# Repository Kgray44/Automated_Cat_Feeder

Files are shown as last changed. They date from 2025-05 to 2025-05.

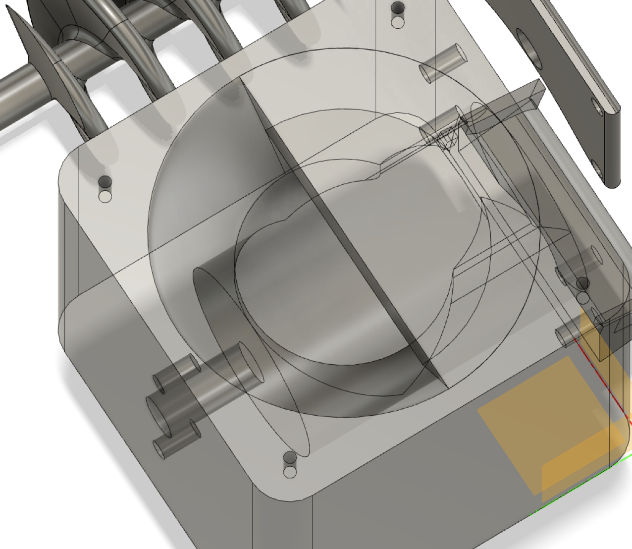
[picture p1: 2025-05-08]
Pictures/3D/image.png

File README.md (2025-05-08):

# Automated_Cat_Feeder
An automated cat feeder project based on an ESP32!

## Project Components
* DRV8874 motor driver
* TPS65261 3-channel voltage regulator
* ESP32-S3-WROOM-1 with 8MB RAM
* OV2640 camera
* I2C OLED Display

## Project Overview
* Feeds cats using an auger design
* Has a food hopper for long term dispension
* Automated system with schedule and facial recognition
* Manual option for feeding immediately
* Utilizes WiFi for UI and obtaining the current time
* Smooth WiFi setup interface for new networks

## Project Status (as of 5/8/25)
* Partially working auger system for dispensing
* Working motor driver / motor system with current feedback
* Working jam detection using current feedback from motor
* Easy to use web interface containing settings; feed time length, a schedule (4x a day max), a change password page, a page to reset device or erase memory, and a page to update software, etc.
* Smooth WiFi setup for first time network connection with multiple fallbacks
* Working OLED display displaying feeder status

## How to Use
Upload the code from the respository to your cat feeder board.  Power up the device and then refer to the 'WiFi Setup' section for next steps.

## Project Description

### WiFi Setup
When first turning the system on, the board will check its flash for a saved network.  If there is a saved network, it will attempt to connect to it. If it can't connect after 30 sec, it will erase the saved network from flash, and restart itself.  If there is no saved network in flash, it will start an access point network called 'catfeeder_AP'.  After connecting to this network with your smartphone (laptop/dekstop works as well, but you must go to '192.168.4.1' in a browser), a captive portal will come up requiring you to put in a network name and password.  After you have entered these, the device will reboot, and attempt to connect to that network.

### User Interface (website)
If the WiFi connection is successful, go to 'catfeeder.local' in a browser, and a webpage will open requiring you to signin.  Trying to visit any of the feeder's webpages without signing in will kick you back to the signin page.  After successfully signing in, the home page will load which contains a menu bar, two main settings, and a 'feed now' button.  There is also an LED indicator that will turn green when the motor is running, and stay red when not.

All webpages that you open on this webpage will be loaded next to the homepage dynamically.  The page will never reload, nor should you need to reload it for any reason.  All data and pages are delivered dynamically and updated automatically.

### Siri Integration (for iPhone/Mac)
By adding a shortcut to your device, you can use "Hey Siri" to turn the feeder on*.  It utilizes the cookie authentication to be able to turn the device on with the '/feed' endpoint.  To call this shortcut, say "Hey Siri" and then the shortcut name.  I named my shortcut 'Feed my Cats', so I would say "Hey Siri, feed my cats".
Visit this link to retrieve the shortcut: https://www.icloud.com/shortcuts/d3358b3d90564f18b419d0107f0d7751

*Please note this only works when on the same WiFi network as the feeder itself.

## Unfinished Components / Issues (as of 5/8/25)
* I am still working on getting the camera to work, so no facial recognition or camera code is added yet
* Auger currently jams due to bad screw design
* OLED Display displays "feeding" even when not feeding
* Food measurement is currently in seconds the auger turns, instead of grams of food
* A small box appears next to the homepage after going to another webpage and going back

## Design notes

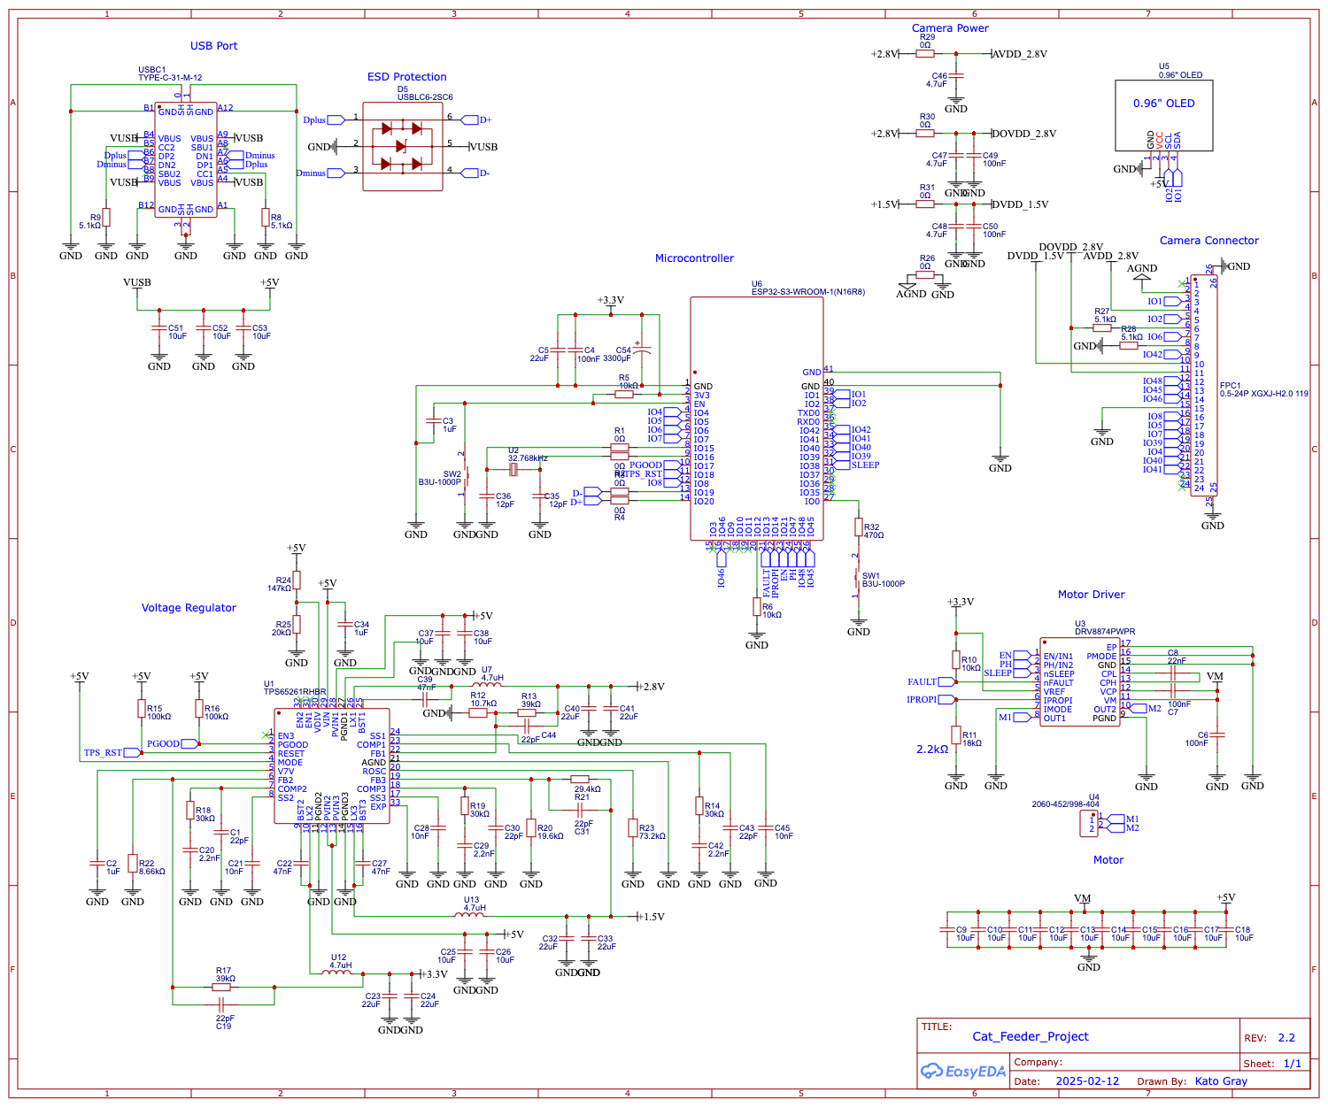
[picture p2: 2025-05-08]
design_files/schematic/Schematic_Cat Feeder Project 2_2025-05-08.png

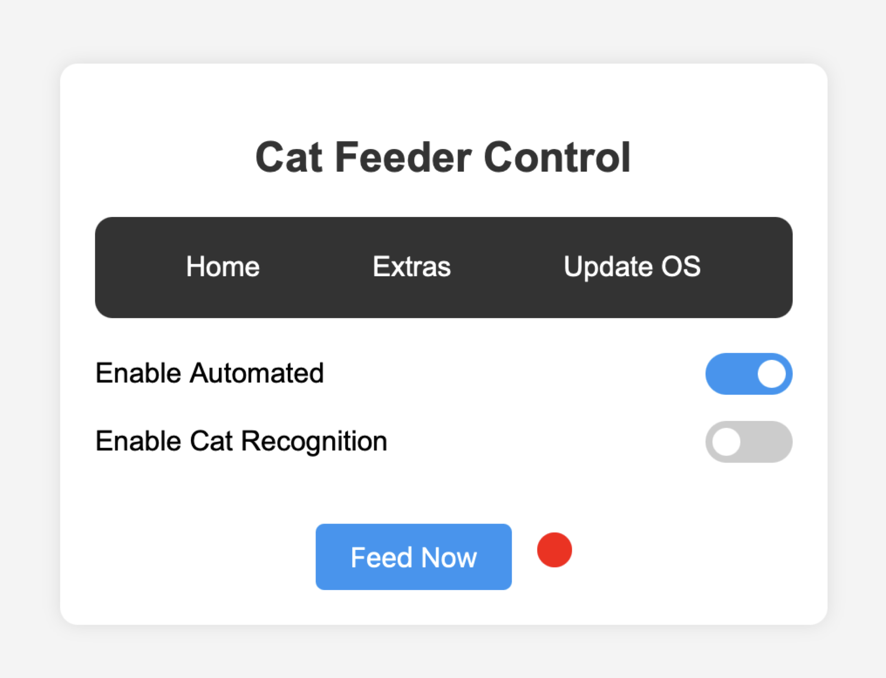
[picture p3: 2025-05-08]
Pictures/website/homepage.png

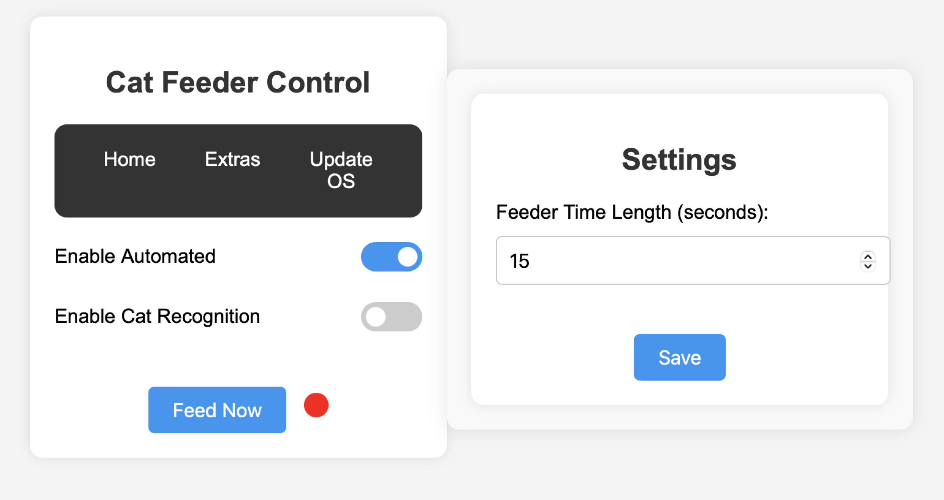
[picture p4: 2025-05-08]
Pictures/website/image.png

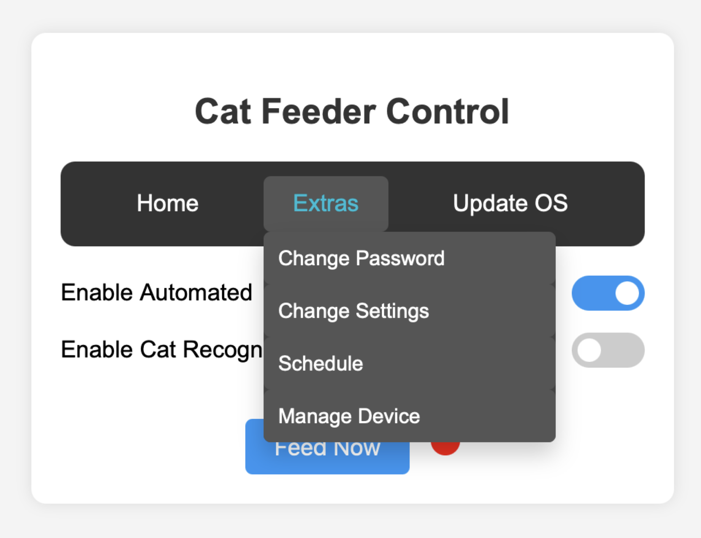
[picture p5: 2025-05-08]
Pictures/website/menu.png

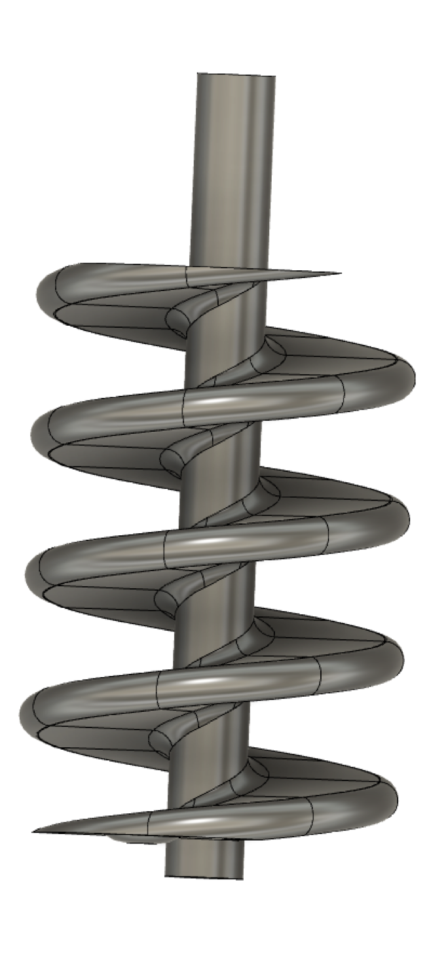
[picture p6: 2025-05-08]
Pictures/3D/screw.png

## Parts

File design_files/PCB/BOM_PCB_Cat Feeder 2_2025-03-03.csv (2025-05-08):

ID | Name | Designator | Footprint | Quantity | Manufacturer Part | Manufacturer | Supplier | Supplier Part | Price
1 | 22pF | C1,C19,C30,C31,C43,C44 | C0402 | 6 | CC0402GRNPO9BN220 | YAGEO(国巨) | LCSC | C541412 | 0.002
2 | 1uF | C2,C3,C34 | C0402 | 3 | CL05A105KO5NNNC | SAMSUNG(三星) | LCSC | C29266 | 0.002
3 | 100nF | C4,C6,C7,C49,C50 | C0402 | 5 | CL05B104KO5NNNC | SAMSUNG(三星) | LCSC | C1525 | 0.001
4 | 22nF | C8 | C0402 | 1 | GRM155R71E223JA61D | muRata(村田) | LCSC | C426639 | 0.011
5 | 2.2nF | C20,C29,C42 | C0402 | 3 | CC0402JRX7R9BB222 | YAGEO(国巨) | LCSC | C513667 | 0.002
6 | 10nF | C21,C28,C45 | C0402 | 3 | CC0402JRX7R9BB103 | YAGEO(国巨) | LCSC | C272878 | 0.002
7 | 47nF | C22,C27,C39 | C0402 | 3 | 0402B473K500NT | FH(风华) | LCSC | C82219 | 0.002
8 | 12pF | C35,C36 | C0402 | 2 | GCM1555C1H120FA16D | muRata(村田) | LCSC | C393682 | 0.018
9 | 22uF | C5 | C0603 | 1 | CL10A226MP8NUNE | SAMSUNG(三星) | LCSC | C86295 | 0.012
10 | 10uF | C25,C26,C37,C38,C51,C52,C53 | C0603 | 7 | CL10A106KP8NNNC | SAMSUNG(三星) | LCSC | C19702 | 0.006
11 | 4.7uF | C46,C47,C48 | C0603 | 3 | CL10A475KP8NNNC | SAMSUNG(三星) | LCSC | C1705 | 0.004
12 | 10uF | C9,C10,C11,C12,C13,C14,C15,C16,C17,C18 | C0805 | 10 | CL21A106KBYQNNE | SAMSUNG(三星) | LCSC | C2932476 | 0.05
13 | 22uF | C23,C24,C32,C33,C40,C41 | C0805 | 6 | CL21A226MOQNNNE | SAMSUNG(三星) | LCSC | C98190 | 0.019
14 | USBLC6-2SC6 | D5 | SOT-23-6_L2.9-W1.6-P0.95-LS2.8-BL | 1 | USBLC6-2SC6 | ST(意法半导体) | LCSC | C7519 | 0.111
15 | 0.5-24P XGXJ-H2.0 119 | FPC1 | FPC-SMD_24P-P0.50_SHOU-HAN_XGXJ-H2.0 | 1 | 0.5-24P XGXJ-H2.0 119 | SHOU HAN(首韩) | LCSC | C2858298 | 0.101
16 | 0Ω | R1,R2,R3,R4,R26,R29,R30,R31 | R0402 | 8 | 0402WGF0000TCE | UNI-ROYAL(厚声) | LCSC | C17168 | 0.001
17 | 10kΩ | R5,R6,R10 | R0402 | 3 | 0402WGJ0103TCE | UNI-ROYAL(厚声) | LCSC | C25531 | 0.001
18 | 5.1kΩ | R8,R9,R27,R28 | R0402 | 4 | 0402WGF5101TCE | UNI-ROYAL(厚声) | LCSC | C25905 | 0.001
19 | 18kΩ | R11 | R0402 | 1 | RT0402BRD0718KL | YAGEO(国巨) | LCSC | C852579 | 0.021
20 | 10.7kΩ | R12 | R0402 | 1 | PTFR0402B10K7N9 | RESI(开步睿思) | LCSC | C2693084 | 0.109
21 | 39kΩ | R13,R17 | R0402 | 2 | RC0402FR-0739KL | YAGEO(国巨) | LCSC | C137995 | 0.001
22 | 30kΩ | R14,R18,R19 | R0402 | 3 | RC0402FR-0730KL | YAGEO(国巨) | LCSC | C138008 | 0.001
23 | 100kΩ | R15,R16 | R0402 | 2 | RC0402FR-07100KL | YAGEO(国巨) | LCSC | C60491 | 0.001
24 | 19.6kΩ | R20 | R0402 | 1 | RT0402BRD0719K6L | YAGEO(国巨) | LCSC | C852589 | 0.021
25 | 29.4kΩ | R21 | R0402 | 1 | 0402WGF2942TCE | UNI-ROYAL(厚声) | LCSC | C26973 | 0.001
26 | 8.66kΩ | R22 | R0402 | 1 | FRC0402F8661TS | FOJAN(富捷) | LCSC | C5126133 | 0.001
27 | 73.2kΩ | R23 | R0402 | 1 | RT0402BRD0773K2L | YAGEO(国巨) | LCSC | C852909 | 0.02
28 | 147kΩ | R24 | R0402 | 1 | 0402WGF1473TCE | UNI-ROYAL(厚声) | LCSC | C64171 | 0.001
29 | 20kΩ | R25 | R0402 | 1 | RC0402FR-0720KL | YAGEO(国巨) | LCSC | C93942 | 0.001
30 | 470Ω | R32 | R0402 | 1 | RC0402FR-07470RL | YAGEO(国巨) | LCSC | C114877 | 0.001
31 | B3U-1000P | SW1 | KEY-SMD_B3U-1000PM | 1 | B3U-1000P | OMRON(欧姆龙) | LCSC | C231329 | 0.159
32 | TPS65261RHBR | U1 | VQFN-32_L5.0-W5.0-P0.50-TL-EP | 1 | TPS65261RHBR | TI(德州仪器) | LCSC | C138722 | 0.548
33 | 32.768kHz | U2 | CRYSTAL-SMD_L3.2-W1.5 | 1 | FC31M2-32.768-NTLNNDTL | HCI(杭晶) | LCSC | C5120559 | 0.19
34 | DRV8874PWPR | U3 | HTSSOP-16_L5.0-W4.4-P0.65-LS6.4-BL-EP | 1 | DRV8874PWPR | TI(德州仪器) | LCSC | C1855818 | 0.88
35 | 2060-452/998-404 | U4 | CONN-SMD_2060-452 | 1 | 2060-452/998-404 | WAGO(万可) | LCSC | C2765055 | 0.236
36 | 0.96" OLED | U5 | CONN-TH_PZ2.54-1X4-11.2 | 1
37 | ESP32-S3-WROOM-1(N16R8) | U6 | WIRELM-SMD_ESP32-S3-WROOM-1 | 1 | ESP32-S3-WROOM-1-N16R8 | ESPRESSIF(乐鑫) | LCSC | C2913202 | 5.774
38 | 4.7uH | U7,U12,U13 | IND-SMD_L5.2-W5.2_MS0530-XX | 3 | MDA5030-4R7M | KOHERelec(科或) | LCSC | C2847477 | 0.825
39 | TYPE-C-31-M-12 | USBC1 | USB-C_SMD-TYPE-C-31-M-12 | 1 | TYPE-C-31-M-12 | 韩国韩荣 | LCSC | C165948 | 0.175

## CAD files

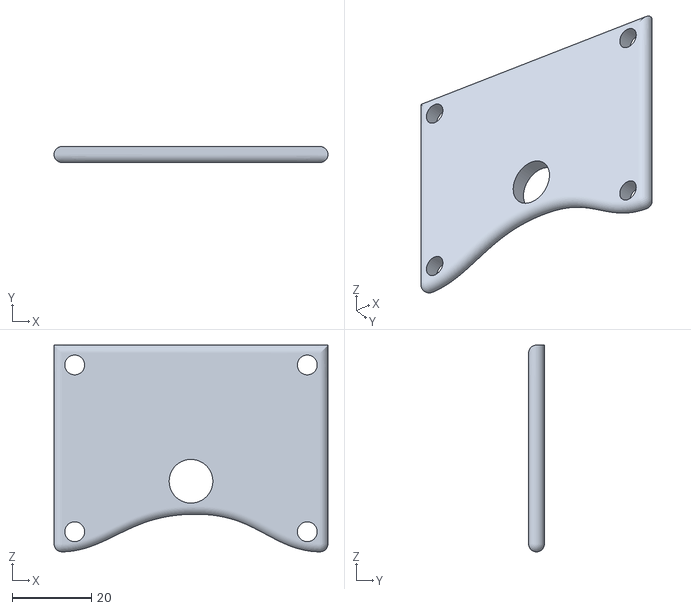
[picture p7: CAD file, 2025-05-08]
design_files/3D_fusion/Lid.stl
69.0 x 4.00 x 52.1

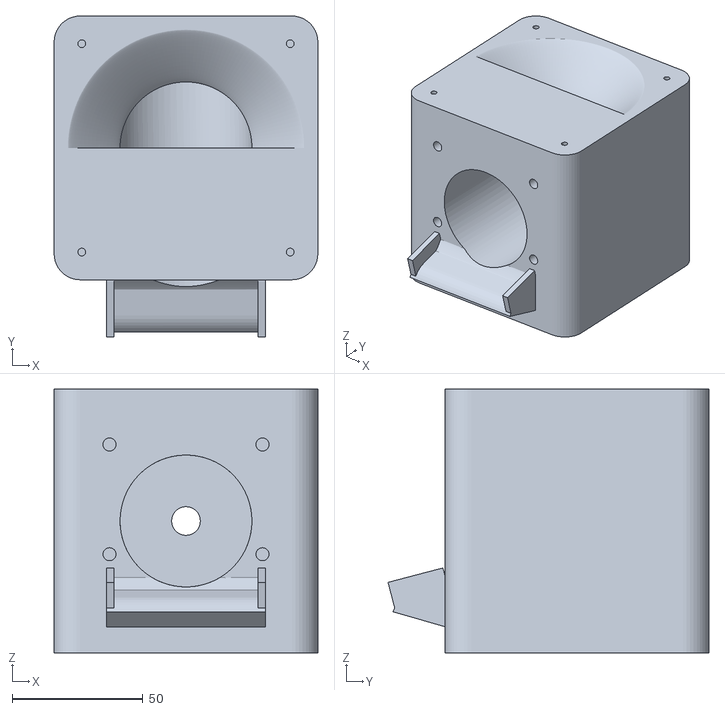
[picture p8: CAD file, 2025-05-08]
design_files/3D_fusion/Body1 (new).stl
101.0 x 122.9 x 101.0

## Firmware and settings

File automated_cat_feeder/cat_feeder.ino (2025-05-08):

#include <WiFi.h>
#include <WiFiAP.h>
#include "esp_wifi.h"
#include <DNSServer.h>
#include <HTTPClient.h>
#include <AsyncTCP.h>
#include <ESPAsyncWebServer.h>
#include <Update.h>
#include <ESPmDNS.h>
#include <ArduinoJson.h>
#include <map>
#include <vector>
#include <time.h>
#include <Preferences.h>
#include <SPI.h>
#include <Wire.h>
#include <Adafruit_GFX.h>
#include <Adafruit_SSD1306.h>
#include <Fonts/FreeSerif9pt7b.h>

#include "html.h"
#include "bitmap_icons.h"

//motor driver pins
#define PGOOD     17  //IO17
#define PRST      18  //IO18
#define sleep_pin 38  //IO38
#define en_pin    21  //IO21
#define ph_pin    47  //IO47
#define fault_pin 13  //IO13
#define ipropi    14  //IO14

#define SCREEN_WIDTH    128   // OLED display width, in pixels
#define SCREEN_HEIGHT   64    // OLED display height, in pixels
#define OLED_RESET      -1    // Reset pin # (or -1 if sharing Arduino reset pin)
#define SCREEN_ADDRESS  0x3C ///< See datasheet for Address; 0x3D for 128x64, 0x3C for 128x32
#define SDA 1
#define SCL 2

#define jamcurrent 350 //current in mA for jam
#define jamFixAttemptLimit 10 //number of attempts to fix the jam

bool jammed = false;
int jamFixAttempt = 0;
float smoothedCurrent_mA = 0;
float smoothingFactor = 0.1;  // smaller = smoother

// Wi-Fi Configuration
const char* ssid = "";//don't fill
const char* password = "";//don't fill
const char* ap_ssid = "catfeeder_AP";
const char* ap_password = "makers4ever";

// Login credentials
const char* login_username = "cats";
const char* login_password = "maker";

bool automated = false;
bool cat_recognition = false;
bool motorOn = false;
bool feeder_on = false;
unsigned long startmillis = 0;
unsigned long lastms2 = 0;
unsigned long scheduleMillis = 0;
unsigned long setupmillis = 0;
unsigned long internetmillis = 0;
unsigned long lastSend = 0;
int motorTime = 5;

bool tog=false;
bool printed=false;

//WiFi AP
const byte DNS_PORT = 53;
IPAddress apIP(192, 168, 4, 1); // SoftAP IP
DNSServer dnsServer;

Adafruit_SSD1306 display(SCREEN_WIDTH, SCREEN_HEIGHT, &Wire, OLED_RESET);

// Async Web Server
AsyncWebServer server(80);
AsyncWebSocket ws("/ws");

bool isAuthenticated(AsyncWebServerRequest *request) {
  if (request->hasHeader("Cookie")) {
    String cookie = request->header("Cookie");
    if (cookie.indexOf("ESPSESSIONID=1") != -1) {
      return true;
    }
  }
  return false;
}

void notifyClients() {
  String json = "{\"automated\":";
  json += automated ? "true" : "false";
  json += ",\"cat_recognition\":";
  json += cat_recognition ? "true" : "false";
  json += ",\"motorOn\":";
  json += motorOn ? "true" : "false";
  json += ",\"current\":";
  json += smoothedCurrent_mA;
  json += "}";
  ws.textAll(json);
  Serial.println(json);
}

void handleWebSocketMessage(void *arg, uint8_t *data, size_t len) {
  AwsFrameInfo *info = (AwsFrameInfo *)arg;
  if (info->final && info->index == 0 && info->len == len && info->opcode == WS_TEXT) {
    data[len] = 0;
    if (strcmp((char *)data, "toggleAutomated") == 0) {
      Serial.println("toggleAutomated");
    } else if (strcmp((char *)data, "toggleCat_recognition") == 0) {
      Serial.println("toggleCat_recognition");
    } else if (strcmp((char *)data, "getStatus") == 0) {
      // If the client requests the status, send it
      notifyClients();
      Serial.println("Sent status update to client");
    }
    notifyClients();
    Serial.println("handled websocket message...");
  }
}

void onEvent(AsyncWebSocket *server, AsyncWebSocketClient *client, AwsEventType type,
             void *arg, uint8_t *data, size_t len) {
  switch (type) {
    case WS_EVT_CONNECT:
      Serial.println("WebSocket client connected");
      notifyClients();
      break;
    case WS_EVT_DISCONNECT:
      Serial.println("WebSocket client disconnected");
      break;
    case WS_EVT_DATA:
      handleWebSocketMessage(arg, data, len);
      break;
    case WS_EVT_PONG:
    case WS_EVT_ERROR:
      break;
  }
}

String makeScheduleRows() {
  String days[] = {"Sun","Mon","Tue","Wed","Thu","Fri","Sat"};
  String html;
  for (int d = 0; d < 7; d++) {
    html += "<tr><td>" + days[d] + "</td><td class='time-slot'>";
    for (int i = 0; i < 4; i++) {
      html += "<input type='time' id='" + days[d] + String(i) + "' name='" + days[d] + String(i) + "'>";
    }
    html += "</td></tr>";
  }

  return html;
}

String schedule_processor(const String& var) {
  if (var == "SCHEDULE_ROWS") {
    String rows = makeScheduleRows();
    return String(rows);
  }
  return String(); // Return empty string for unknown placeholders
}

/*String motortime_processor(const String& var) {
  if (var == "MOTORTIME"){
    return String(motorTime);
  }
  return String();
}*/

bool checkInternet() {
  if (WiFi.status() != WL_CONNECTED) return false;

  HTTPClient http;
  http.setConnectTimeout(3000);  // 3 sec timeout
  http.begin("http://clients3.google.com/generate_204");  // Lightweight, returns 204
  int code = http.GET();
  http.end();

  return (code == 204);
}

std::map<String, std::vector<String>> feedingSchedule;
Preferences prefs;

void setup() {
  Serial.begin(115200);
  esp_reset_reason_t reason = esp_reset_reason();
  Serial.printf("\nReset reason: %d → ", reason);
  switch (reason) {
    case ESP_RST_POWERON:      Serial.println("POWERON_RESET"); break;
    case ESP_RST_EXT:          Serial.println("EXT_RESET"); break;
    case ESP_RST_SW:           Serial.println("SW_RESET"); break;
    case ESP_RST_PANIC:        Serial.println("PANIC_RESET"); break;
    case ESP_RST_INT_WDT:      Serial.println("INT_WDT_RESET"); break;
    case ESP_RST_TASK_WDT:     Serial.println("TASK_WDT_RESET"); break;
    case ESP_RST_WDT:          Serial.println("OTHER_WDT_RESET"); break;
    case ESP_RST_DEEPSLEEP:    Serial.println("DEEPSLEEP_RESET"); break;
    case ESP_RST_BROWNOUT:     Serial.println("BROWNOUT_RESET"); break;
    case ESP_RST_SDIO:         Serial.println("SDIO_RESET"); break;
    case ESP_RST_USB:          Serial.println("USB_RESET"); break;
    default:                   Serial.println("UNKNOWN"); break;
  } 

  Wire.begin(SDA, SCL);
  delay(100);

  if(!display.begin(SSD1306_SWITCHCAPVCC, SCREEN_ADDRESS)) {
    Serial.println(F("SSD1306 allocation failed"));
  }
  //display.setFont(&FreeSerif9pt7b);
  display.clearDisplay();

  pinMode(sleep_pin, OUTPUT);
  pinMode(en_pin, OUTPUT);
  pinMode(ph_pin, OUTPUT);
  pinMode(fault_pin, INPUT);
  pinMode(ipropi, INPUT);
  pinMode(PGOOD, INPUT);
  pinMode(PRST, INPUT);

  digitalWrite(sleep_pin, LOW);//turn sleep on
  //digitalWrite(en_pin, HIGH);//enable
  Serial.println("Pins setup complete!\nStarting WiFi...");

  //load saved data from flash memory
  loadSavedData();

  if (strlen(ssid) > 0){
    // Initialize Wi-Fi
    WiFi.mode(WIFI_STA);
    WiFi.begin(ssid, password);
    setupmillis = millis();
    Serial.print("Connecting to WiFi");
    while (WiFi.status() != WL_CONNECTED) {
      delay(500);
      Serial.print(".");
      if (tog){printCentered("WiFi STA .");} else {printCentered("WiFi STA  ");}
      tog=!tog;
      if (millis() - setupmillis > 20000){//20 seconds not connecting
        prefs.begin("wifi_network", false);
        prefs.putString("ssid", "");
        prefs.putString("pass", "");
        prefs.end();

        Serial.println("Rebooting now due to failed connection...");
        printCentered("Failed connection!");
        delay(2000);
        ESP.restart();
      }
    }
    Serial.println("\nConnected to WiFi");
    Serial.println("IP Address:");
    Serial.println(WiFi.localIP());
    printCentered("WiFi Connected\n'catfeeder.local'");
    delay(500);
  
  // Set time zone and NTP server
  //configTzTime("EST5EDT,M3.2.0/2,M11.1.0/2", "pool.ntp.org", "time.nist.gov");
  configTime(-4 * 3600, 0, "pool.ntp.org", "time.nist.gov");
  Serial.print("Waiting for time sync");

  setupmillis = millis();
  time_t now = time(nullptr);

  while (now < 8 * 3600 * 2 && (millis() - setupmillis < 20000)) {
    if (tog){printCentered("WiFi Connected\n'catfeeder.local'\nTime sync .");} else {printCentered("WiFi Connected\n'catfeeder.local'\nTime sync  ");}
    tog=!tog;
    delay(500);
    Serial.print(".");
    now = time(nullptr);
  }

  if (now < 8 * 3600 * 2) {
    Serial.println("\n Time sync failed after 20 seconds.");
    printCentered("Time sync failed!");
    delay(2000);
  } else {
    Serial.println("\n Time synchronized.");
    printCentered("WiFi Connected\n'catfeeder.local'\nTime sync success!");
    struct tm* t = localtime(&now);
    char currentTime[6];
    sprintf(currentTime, "%02d:%02d", t->tm_hour, t->tm_min);
    Serial.println(currentTime);
  }

  ws.onEvent(onEvent);
  server.addHandler(&ws);

  server.on("/", HTTP_GET, [](AsyncWebServerRequest *request) {
    if (isAuthenticated(request)) {
      request->redirect("/index");
      notifyClients();
    } else {
      request->send_P(200, "text/html", login_html);
    }
  });

  // Route to Handle Login
  server.on("/login", HTTP_POST, [](AsyncWebServerRequest *request) {
    if (request->hasParam("username", true) && request->hasParam("password", true)) {
      String username = request->getParam("username", true)->value();
      String password = request->getParam("password", true)->value();
      if (username == login_username && password == login_password) {
        AsyncWebServerResponse *response = request->beginResponse(301);
        response->addHeader("Set-Cookie", "ESPSESSIONID=1; HttpOnly");
        response->addHeader("Location", "/index");
        request->send(response);
      } else {
        request->send(401, "text/plain", "Unauthorized");
      }
    }
  });

  // Route for Control Page
  server.on("/index", HTTP_GET, [](AsyncWebServerRequest *request) {
    if (isAuthenticated(request)) {
      request->send_P(200, "text/html", index_html);
      notifyClients();
    } else {
      request->redirect("/");
    }
  });

  //route for password change
  server.on("/change", HTTP_GET, [](AsyncWebServerRequest *request) {
    if (isAuthenticated(request)) {
      request->send_P(200, "text/html", change_html);
    } else {
      request->redirect("/");
    }
  });

  server.on("/save-change", HTTP_POST, [](AsyncWebServerRequest *request) {
    if (request->hasParam("password", true) && request->hasParam("passwordd", true)) {
      String password = request->getParam("password", true)->value();
      String passwordd = request->getParam("passwordd", true)->value();

      if (password == passwordd) {
        // Save the new password logic here
        login_password = password.c_str();
        prefs.begin("auth", false);
        prefs.putString("password", login_password);
        prefs.end();
        request->send(200, "text/plain", "Password successfully changed.");
      } else {
        request->send(400, "text/plain", "Passwords do not match.");
      }
    } else {
      request->send(400, "text/plain", "Missing parameters.");
    }
  });

  //route for settings
  server.on("/settings", HTTP_GET, [](AsyncWebServerRequest *request) {
    if (isAuthenticated(request)) {
      request->send(200, "text/html", settings_html);
    } else {
      request->redirect("/");
    }
  });

  server.on("/save-settings", HTTP_POST, [](AsyncWebServerRequest *request) {
    if (!isAuthenticated(request)) {
      request->send(401, "text/plain", "Unauthorized");
      return;
    }

    if (request->hasParam("motorTime", true)) {
      String motorTimeR = request->getParam("motorTime", true)->value();
      motorTime = motorTimeR.toInt();
      Serial.println("Motor Time Length updated to: " + String(motorTime));

      prefs.begin("settings", false); // namespace = "settings", readWrite = false
      prefs.putInt("motorTime", motorTime);
      prefs.end();

      request->send(200, "text/plain", "Settings saved successfully!");
      //request->redirect("/index");
    } else {
      request->send(400, "text/plain", "Motor Time Length not provided");
    }
  });

  server.on("/api/motortime", HTTP_GET, [](AsyncWebServerRequest *request){
    if (!isAuthenticated(request)) {
      request->send(401, "application/json", "{\"error\":\"unauthorized\"}");
      return;
    }
    request->send(200, "application/json", "{\"motorTime\":" + String(motorTime) + "}");
  });

  /*server.on("/schedule", HTTP_GET, [](AsyncWebServerRequest *request){
    if (!isAuthenticated(request)) {
      request->redirect("/");
      return;
    }
    String html = String(schedule_html);
    html.replace("%SCHEDULE_ROWS%", makeScheduleRows());
    request->send(200, "text/html", html);
  });*/
  server.on("/schedule", HTTP_GET, [](AsyncWebServerRequest *request){
    if (!isAuthenticated(request)) {
      request->redirect("/");
      return;
    }
    request->send(200, "text/html", schedule_html, schedule_processor);
  });


  server.on("/save-schedule", HTTP_POST, [](AsyncWebServerRequest *request){
    if (!isAuthenticated(request)) {
      request->send(401, "text/plain", "Unauthorized");
      return;
    }
  }, NULL, [](AsyncWebServerRequest *request, uint8_t *data, size_t len, size_t index, size_t total) {
    StaticJsonDocument<2048> doc;
    DeserializationError error = deserializeJson(doc, data, len);

    if (error) {
      request->send(400, "text/plain", "Bad JSON");
      return;
    }

    feedingSchedule.clear();

    for (JsonPair kv : doc.as<JsonObject>()) {
      String day = kv.key().c_str();
      JsonArray times = kv.value().as<JsonArray>();
      for (JsonVariant v : times) {
        feedingSchedule[day].push_back(v.as<String>());
      }
    }
    // 🔒 Save entire schedule JSON to NVS (flash)
    prefs.begin("schedule", false);
    String jsonString;
    serializeJson(doc, jsonString);
    prefs.putString("feedmap", jsonString);
    prefs.end();

    request->send(200, "text/plain", "Schedule saved");
  });
  
  server.on("/api/schedule", HTTP_GET, [](AsyncWebServerRequest *request){
    if (!isAuthenticated(request)) {
      request->send(401, "application/json", "{\"error\":\"unauthorized\"}");
      return;
    }

    StaticJsonDocument<2048> doc;

    for (auto const& kv : feedingSchedule) {
      JsonArray arr = doc.createNestedArray(kv.first);
      for (auto const& time : kv.second) {
        arr.add(time);
      }
    }

    String response;
    serializeJson(doc, response);
    request->send(200, "application/json", response);
  });

  server.on("/reset-schedule", HTTP_POST, [](AsyncWebServerRequest *request){
    if (!isAuthenticated(request)) {
      request->send(401, "text/plain", "Unauthorized");
      return;
    }

    feedingSchedule.clear();  // Clear the stored schedule
    Serial.println("Schedule has been reset.");
    request->send(200, "text/plain", "Schedule reset");
  });

  server.on("/manage", HTTP_GET, [](AsyncWebServerRequest *request) {
    if (isAuthenticated(request)) {
      request->send_P(200, "text/html", manage_html);
    } else {
      request->redirect("/");
    }
  });

  server.on("/reset", HTTP_POST, [](AsyncWebServerRequest *request) {
    if (isAuthenticated(request)) {
      prefs.begin("settings", false); prefs.clear(); prefs.end();
      prefs.begin("schedule", false); prefs.clear(); prefs.end();
      prefs.begin("auth", false); prefs.clear(); prefs.end();
      request->send(200, "text/plain", "Memory erased!");
    } else {
      request->send(401);
    }
  });

  server.on("/restart", HTTP_POST, [](AsyncWebServerRequest *request) {
    if (isAuthenticated(request)) {
      request->send(200, "text/plain", "Restarting...");
      delay(100);  // Ensure response is sent
      ESP.restart();
    } else {
      request->send(401);
    }
  });
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
void loop() {
  if (WiFi.getMode() != WIFI_STA){
    printCentered("Waiting for cred");
    dnsServer.processNextRequest();
    return;
  }

  if (jammed){
    ESP.restart();
  }

  if (millis() - internetmillis > 10000){//check for internet every ten seconds
    if (!checkInternet()) {//if no internet, restart
      prefs.begin("wifi_network", false);
      prefs.putString("ssid", "");
      prefs.putString("pass", "");
      prefs.end();
      Serial.println("No internet, restarting and wiping SSID&PASS...");
      printCentered("Internet failed");
      delay(1000);
      ESP.restart();
    }
    internetmillis = millis();
  }

  ws.cleanupClients();
  delay(50);
  yield();
  if (startmillis != 0 && millis() - startmillis > motorTime*1000) {
    digitalWrite(sleep_pin, LOW);//turn sleep on
    digitalWrite(en_pin, LOW);//disable
    motorOn = false;
    Serial.println("Feeder motor off");
    notifyClients();
    printed=false;
    startmillis = 0;
  }

  if (automated){
    checkSchedule();
  }

  if (millis() - lastSend >= 100) {
    if (motorOn){
      if (!printed){printCentered("Feeding ");printed=true;}
      if (tog){display.drawBitmap(60, 24, motor1Char, 5, 8, WHITE);display.display();} else {display.drawBitmap(60, 24, motor1Char, 5, 8, WHITE);display.display();}
      tog=!tog;
      float adcVoltage = analogRead(ipropi) * (3.3 / 4095.0); // volts
      float motorCurrent = adcVoltage / (0.000455 * 2700.0);      // amps
      //motorCurrent = motorCurrent*1000; //ma
      smoothedCurrent_mA = smoothedCurrent_mA * (1.0 - smoothingFactor) + (motorCurrent * 1000.0) * smoothingFactor;

      if (smoothedCurrent_mA >= jamcurrent){
        digitalWrite(ph_pin, LOW);//direction backwards
        delay(1000);
        digitalWrite(ph_pin, HIGH);//direction backwards
        delay(500);
        jamFixAttempt++;
        if (jamFixAttempt >= jamFixAttemptLimit){
          jammed = true;
          return;
        }
      }

      notifyClients();  // only stream current if motor is on
      lastSend = millis();
    }
    else { printed=false;display.clearDisplay();jamFixAttempt=0;lastSend = millis();}
  }
  
  /*if (digitalRead(fault_pin) == LOW){
    Serial.println("FAULT");
  }*/
  
  /*if (millis() - lastms2 > 100){
    float adcVoltage = analogRead(ipropi) * (3.3 / 4095.0); // volts
    float motorCurrent = adcVoltage / (0.000455 * 2700.0);      // amps
    Serial.print("Current pin: ");
    Serial.println(motorCurrent*1000,2);
    lastms2 = millis();
  }*/
}

void printCentered(const String& fullText) {
  display.clearDisplay();
  display.setTextWrap(false); // Prevent automatic wrapping

  display.setTextSize(1); // REQUIRED: set font size (1–3 typically)
  display.setTextColor(SSD1306_WHITE);
  display.setFont();      // Use built-in font (optional, but good reset)

  // Step 1: Count lines
  int numLines = 1;
  for (unsigned int i = 0; i < fullText.length(); i++) {
    if (fullText[i] == '\n') numLines++;
  }

  // Step 2: Get height of one line
  int16_t x1, y1;
  uint16_t w, h;
  display.getTextBounds("A", 0, 0, &x1, &y1, &w, &h);
  int lineHeight = h + 2;
  int totalHeight = numLines * lineHeight;

  // Step 3: Y offset
  int yStart = (SCREEN_HEIGHT - totalHeight) / 2;

  // Step 4: Draw each line centered
  String currentLine = "";
  int lineNum = 0;

  for (unsigned int i = 0; i <= fullText.length(); i++) {
    char c = fullText[i];
    if (c == '\n' || i == fullText.length()) {
      display.getTextBounds(currentLine, 0, 0, &x1, &y1, &w, &h);
      int xStart = (SCREEN_WIDTH - w) / 2;

      display.setCursor(xStart, yStart + lineNum * lineHeight);
      display.print(currentLine);

      currentLine = "";
      lineNum++;
    } else {
      currentLine += c;
    }
  }

  display.display();
}



void checkSchedule() {
  time_t now = time(nullptr);
  struct tm* t = localtime(&now);
  char currentTime[6];
  sprintf(currentTime, "%02d:%02d", t->tm_hour, t->tm_min);

  String dayStr[] = {"Sun","Mon","Tue","Wed","Thu","Fri","Sat"};
  auto& todayTimes = feedingSchedule[dayStr[t->tm_wday]];

  for (auto& feedTime : todayTimes) {
    if (millis() - scheduleMillis > 60000){//only one trigger per minute
      String fullMessage = "Next feed time is\n" + feedTime;
      printCentered(fullMessage.c_str());
      if (feedTime == String(currentTime)) {
        Serial.println("Scheduled Feed Triggered at " + String(currentTime));
        feed(); // existing feed() function
        scheduleMillis = millis();
        break;
      }
    }
  }
}

void feed() {
  digitalWrite(sleep_pin, HIGH);//turn sleep off
  digitalWrite(en_pin, HIGH);//enable
  digitalWrite(ph_pin, HIGH);//direction
  motorOn = true;
  startmillis = millis();
  Serial.println("Feeding initiated");
  notifyClients();
}

void loadSavedData(){
  prefs.begin("settings", true); // readOnly = true
  motorTime = prefs.getInt("motorTime", 5); // default to 5 seconds if not set
  automated = prefs.getInt("automated", 0);
  cat_recognition = prefs.getInt("cat_recognition", 0);
  prefs.end();

  prefs.begin("schedule", true);
  String saved = prefs.getString("feedmap", "");
  prefs.end();
  if (saved.length() > 0) {
    StaticJsonDocument<2048> doc;
    DeserializationError error = deserializeJson(doc, saved);
    if (!error) {
      for (JsonPair kv : doc.as<JsonObject>()) {
        String day = kv.key().c_str();
        JsonArray times = kv.value().as<JsonArray>();
        for (JsonVariant v : times) {
          feedingSchedule[day].push_back(v.as<String>());
        }
      }
      Serial.println("Feeding schedule loaded from flash.");
    } else {
      Serial.println("Failed to parse saved schedule JSON.");
    }
  }

  prefs.begin("auth", true);
  String savedPassword = prefs.getString("password", "");
  prefs.end();
  if (savedPassword.length() > 0) {
    login_password = savedPassword.c_str();
    Serial.println("Login password restored from flash.");
  }
  
  prefs.begin("wifi_network", true);
  String ssid_str = prefs.getString("ssid", "");
  String pass_str = prefs.getString("pass", "");
  ssid = strdup(ssid_str.c_str());       // safely store heap copy
  password = strdup(pass_str.c_str());   // safely store heap copy
  Serial.print("Loaded SSID: "); Serial.print(ssid); Serial.print(" with password: "); Serial.println(password);
  prefs.end();
}

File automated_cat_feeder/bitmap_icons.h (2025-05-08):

const uint8_t wifiIcon[] = {
  0b00011000,
  0b00111100,
  0b01100110,
  0b11111111,
  0b11111111,
  0b01100110,
  0b00111100,
  0b00011000
};

const uint8_t wifiAPIcon[] = {
  0b00011000,
  0b00111100,
  0b01100110,
  0b11111111,
  0b11100110,
  0b11100110,
  0b00111100,
  0b00011000
};

const uint8_t spinnerFrame1[] = {
  0b00100100,
  0b00000000,
  0b10000010,
  0b00000000,
  0b00000000,
  0b10000010,
  0b00000000,
  0b00100100
};

const uint8_t spinnerFrame2[] = {
  0b00011000,
  0b00100100,
  0b01000010,
  0b10000001,
  0b10000001,
  0b01000010,
  0b00100100,
  0b00011000
};

const uint8_t hazardChar[] = {
  0b00000,
  0b00000,
  0b01110,
  0b11001,
  0b10101,
  0b10011,
  0b01110,
  0b00000
};

const uint8_t motor1Char[] = {
  0b00110,
  0b00110,
  0b00100,
  0b01110,
  0b01110,
  0b01110,
  0b01110,
  0b01110
};

const uint8_t motor2Char[] = {
  0b01100,
  0b01100,
  0b00100,
  0b01110,
  0b01110,
  0b01110,
  0b01110,
  0b01110
};


const uint8_t errorIcon[] = {
  0b00111000,
  0b00111000,
  0b00111000,
  0b00000000,
  0b00000000,
  0b00000000,
  0b00111000,
  0b00111000
};
